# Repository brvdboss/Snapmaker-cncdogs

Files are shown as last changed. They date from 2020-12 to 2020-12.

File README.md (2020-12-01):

# Snapmaker-cncdogs
 clamping dogs for the cnc wasteboard of the snapmaker2
 
 This provides a set of clamping tools to secure your stock on the snapmaker cnc wasteboard.
 There are variants for the small holes (where the screws go to mount the wasteboard) and the larger holes where the provided clamps fit
 
 The spirals are used to put additional pressure on one side and come in different sizes to adjust for all your clamping needs
 For these the "keys" are used to make them universal for every type of hole in the wasteboard.  The smallest spiral is designed so it can be used on the holes closest to the side and still clear the vertical axes.
 
 To tighten the clamps a handle is provided to make that easier with the same keyhole.
 This handle can also be used as a wedge to secure your material.

 An additional version has been added with a through-hole that fits an m4 screw. this allows to fix the "large" dogs & turnkeys to fixed to the board.  This improves the clamping force significantly. and eliminates the risk of the dogs coming loos through vibration.  It does mean clamping is no longer "toolless"
 The screws are countersunk rather deep to minimize the risk of your drill hitting it if you go through the plastic and this also helps with the rigidity as the screwhead provides additional strenght in the doghole.

## Why use this?
If you have a piece of material that you can't clamp from the top down or need to secure from the side, for example to align it more easily.
It's from plastic. If your bits do drill in to this, they probably won't get damaged.

## Overview of elements
- **cornerdog**: element to fix the corner of your material. Both in large and small hole variant. For the large version there is now also a through-hole version.
- **dog**: align on the side of your material. Both in large and small hole variant. For the large version there is now also a through-hole variant.
- **spiralhandle**: handle to tighten the pressurespirals.  You can also use this as a wedge in combination with a dog to the fix the material.
- **turnkey**: the "key" that locks in the holes. Both in a large and small hole variant. For the large version there is now also a through-hole variant.
- **turnkeyspiral**: the actual pressure spiral, insert a key, put it in the hole and turn with the spiralhandle.  Different sizes available

Where possible all objects are parameterized so they can easily be adjusted in size
There are no throughole variants of the small versions of the clamps as those holes are used to mount the wasteboard.

## What to watch out for when using this
- These clamps only apply pressure from the side. Depending on the material, tolerance in your dogholes.  Often the material has a tendency to be pushed upwards.  The through hole versions mostly minimize this, but require M4 screws
- The holes in the waste board are small and not very deep, in addition the waste board is rather soft.  Don't put huge amounts of pressure on it.
- When fixing your material also push it down while clamping and check you push the dogs down to make sure everything is secure. You could use one of the snapmaker provide clamps to push down on the pressure weels to get some more downforce on the material.
- You can use the M4 screws included with the snapmaker to fixate the through-hole versions. They are just long enough, a tiny bit longer would have been conventient though.

## How to print
Printing everything using the defaul fast profile in Luban seems to work fine and everything fits snuggly together. (tested with snapmaker provided white filament)

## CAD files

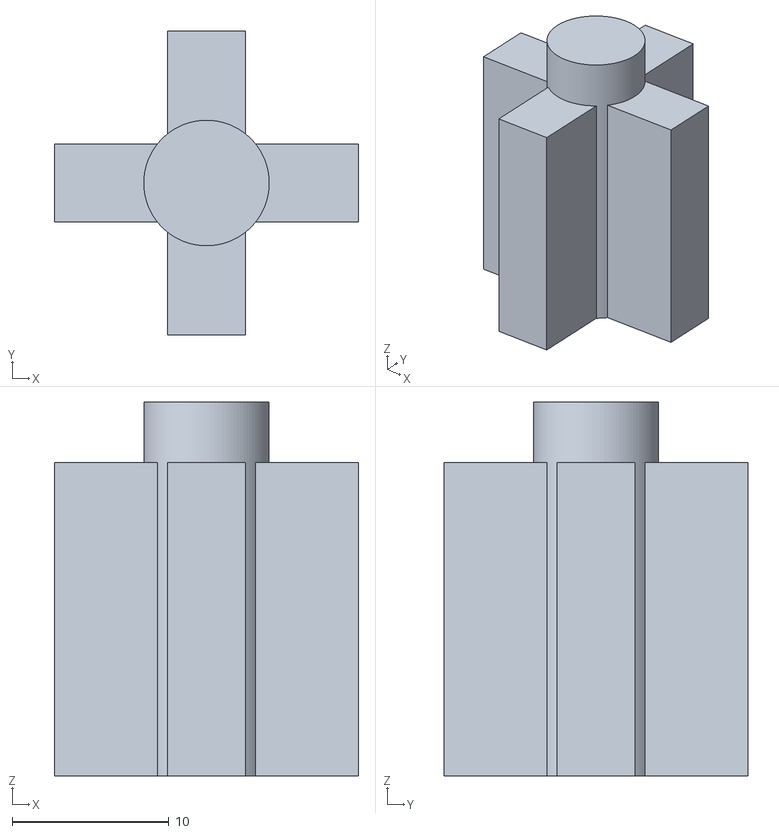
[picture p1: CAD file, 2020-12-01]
stl/turnkeysmall.stl
19.4 x 19.4 x 23.9

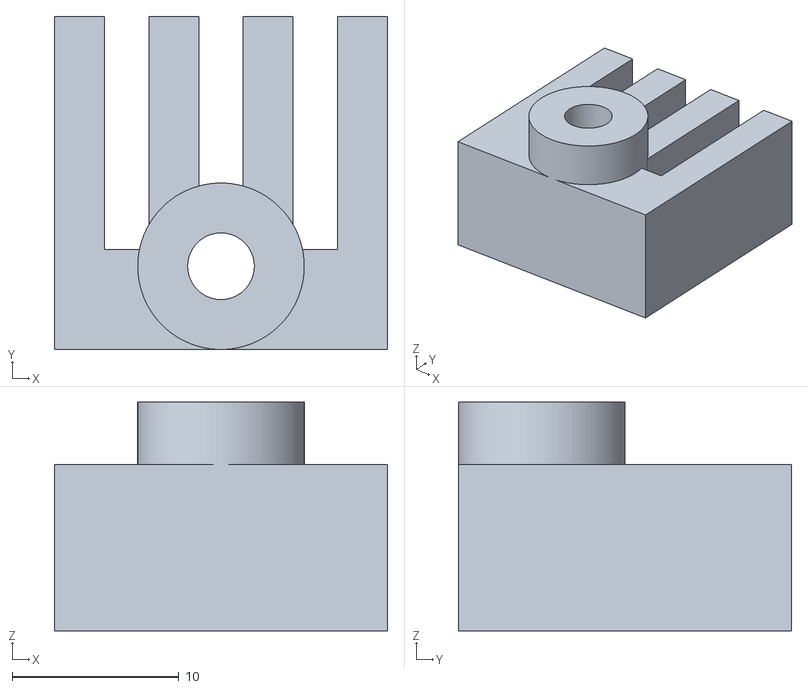
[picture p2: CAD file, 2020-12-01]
stl/doglarge-hole.stl
20.0 x 20.0 x 13.8

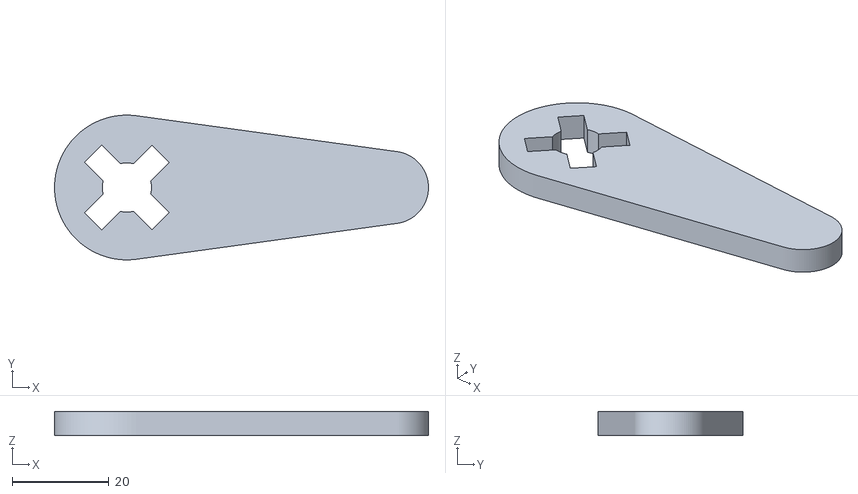
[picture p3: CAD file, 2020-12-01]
stl/spiralhandle.stl
77.5 x 30.0 x 5.00

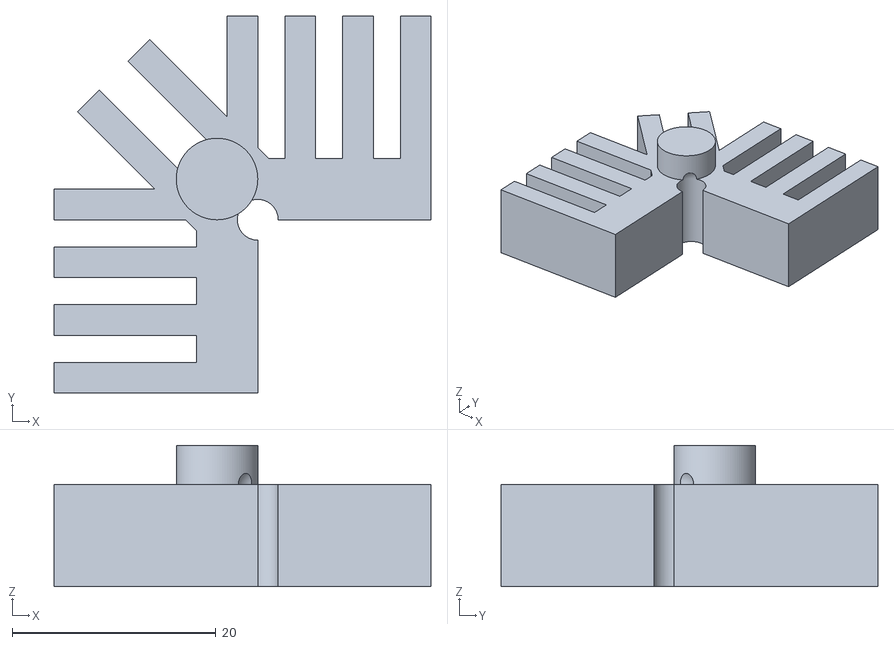
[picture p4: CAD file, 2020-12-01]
stl/cornerdogsmall.stl
37.0 x 37.0 x 13.8

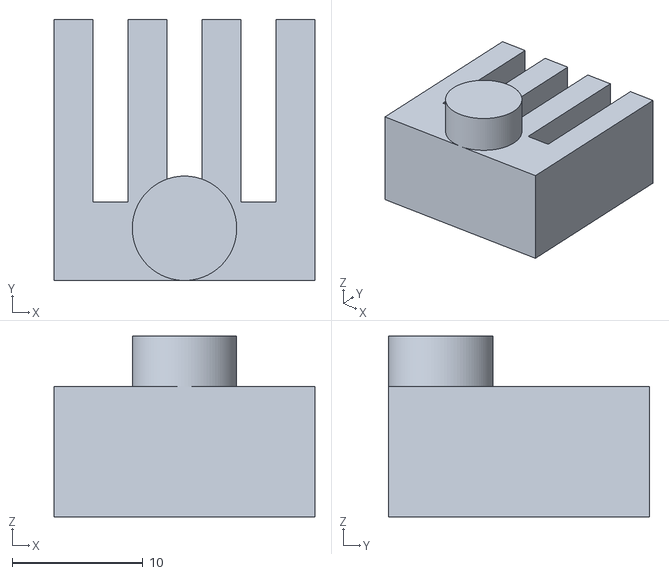
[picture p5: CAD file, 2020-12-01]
stl/dogsmall.stl
20.0 x 20.0 x 13.8

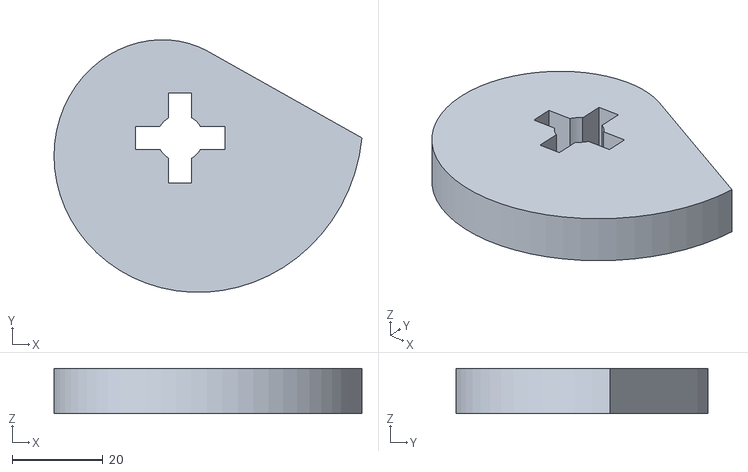
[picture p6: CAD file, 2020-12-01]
stl/turnkeyspiral-40_15.stl
67.8 x 55.5 x 10.0

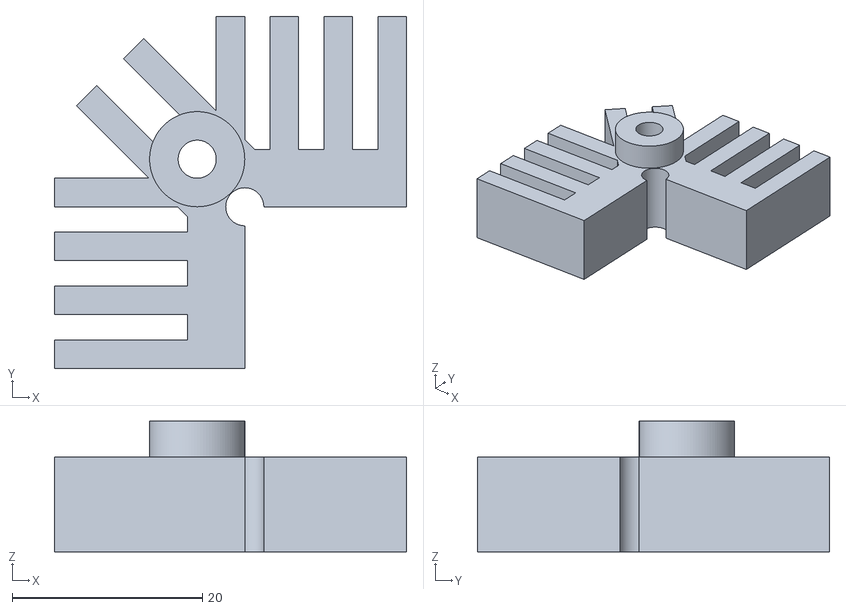
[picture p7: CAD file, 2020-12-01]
stl/cornerdoglarge-hole.stl
37.0 x 37.0 x 13.8

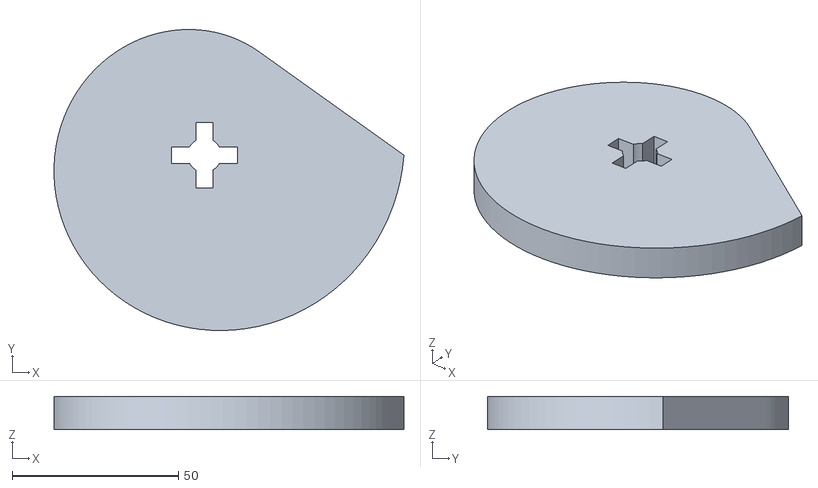
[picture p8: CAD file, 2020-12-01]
stl/turnkeyspiral-60_30.stl
105.2 x 90.5 x 10.0

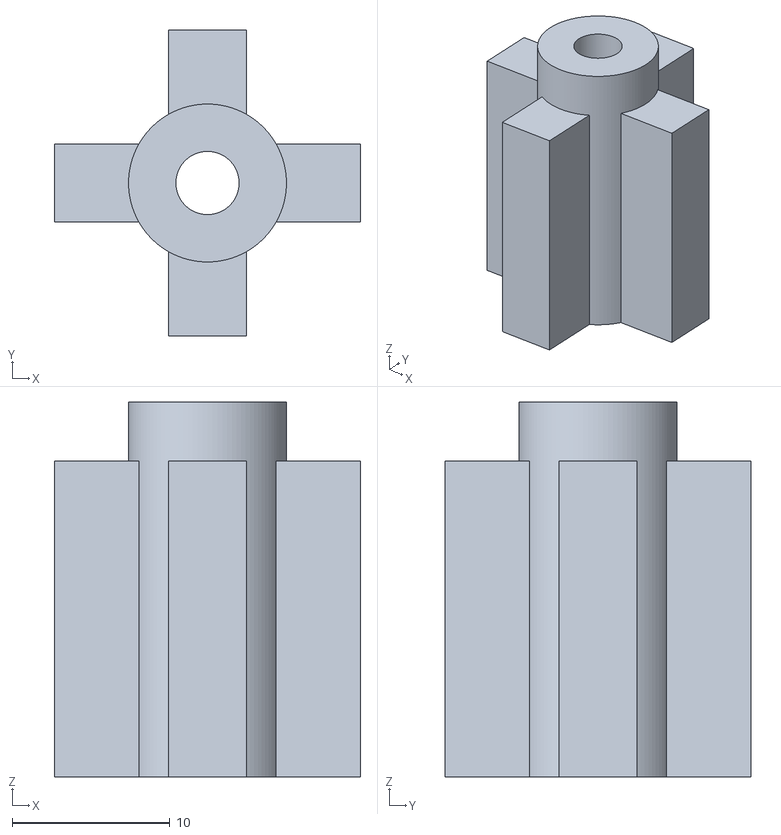
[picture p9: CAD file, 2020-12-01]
stl/turnkeylarge-hole.stl
19.4 x 19.4 x 23.8

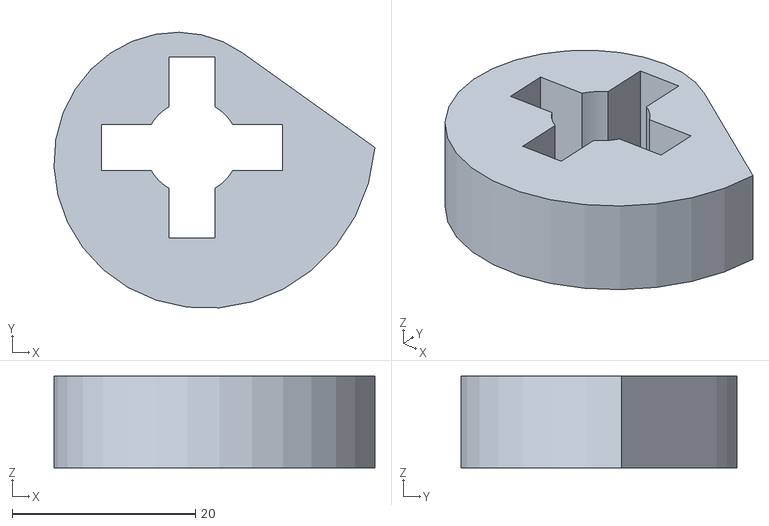
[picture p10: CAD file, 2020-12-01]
stl/turnkeyspiral-20_10.stl
35.1 x 30.1 x 10.0

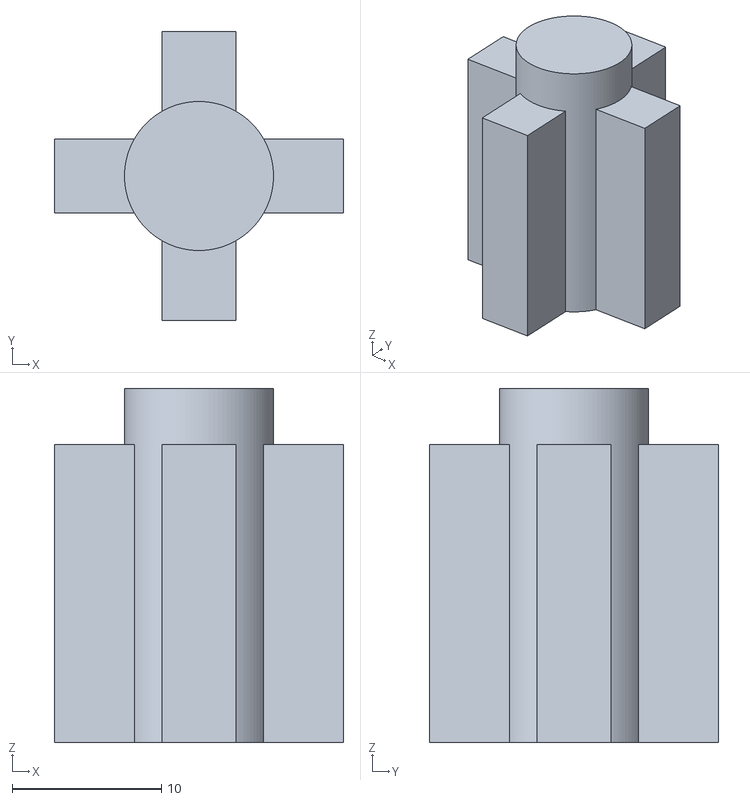
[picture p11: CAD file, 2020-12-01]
stl/turnkeylarge.stl
19.4 x 19.4 x 23.8

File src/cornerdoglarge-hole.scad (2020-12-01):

include <lib/dogs.scad>

cornerdog(dogblock, type="large", hole=true);

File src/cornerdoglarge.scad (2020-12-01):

include <lib/dogs.scad>

cornerdog(dogblock, type="large", hole=false);

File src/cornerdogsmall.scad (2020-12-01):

include <lib/dogs.scad>

cornerdog(dogblock, type="small", hole=false);

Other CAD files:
stl/doglarge.stl
stl/cornerdoglarge.stl
src/doglarge-hole.scad
src/doglarge.scad
src/dogsmall.scad
src/spiralhandle.scad
src/turnkeylarge-hole.scad
src/turnkeylarge.scad
src/turnkeysmall.scad
src/turnkeyspiral-20_10.scad
src/turnkeyspiral-40_15.scad
src/turnkeyspiral-60_30.scad

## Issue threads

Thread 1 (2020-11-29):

pressure spiral: make flat edges depend on size

brvdboss, 2020-11-29:
The pressure spirals have small flat edges to improve the friction when clamping and prevent them from getting loose from vibrations.  It might be better to have them depend on the total size of the pressure spiral.  They should have a fixed width, now they become wider with a bigger spiral.

brvdboss, 2020-12-01:
The flat edge has been adjusted so that it's max 2mm at the biggest diameter.  This for all sizes of spirals

Closed 2020-12-01.

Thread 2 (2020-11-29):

Make everything through hole so it can be fixed with the screws

brvdboss, 2020-11-29:
It should be possible to make all clamps through hole (instead of using the little guide pin that doesn't serve a real purpose).
The could still be used without a screw.
but on some strategic places we can the still insert a screw  to fix it more better in place. This should also help with keeping things down on the plate.

brvdboss, 2020-12-01:
Through hole versions have been committed and seem to work great. Hardly any upward lift remaining when using the through hole versions

Closed 2020-12-01.

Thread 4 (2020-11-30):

spiral and turnkey don't fit well together

brvdboss, 2020-11-30:
See https://forum.snapmaker.com/t/printed-cnc-clamps-sideways-feedback-welcome/11993/8

too tight of a fit of the spiral & turnkey.  Instead of using a scaling percentage in the code, use absolute size difference.  I don't think it is strictly necessary to have an extreme tight fit of these components. So better be on the safe side.

brvdboss, 2020-12-01:
made some tiny adjustments and remeasured everything extensively.  Everything should fit a expected.  Tolerances are a tiny bit higher now.

Closed 2020-12-01.

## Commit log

2020-11-29 First version of everything
    Initial commit of the dogs collection
    [cornerdoglarge.scad, cornerdoglarge.stl, cornerdogsmall.scad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]
2020-12-01 increase tollerances for fitting parts together
    #4 increase the tolerances on the fitting of the spiral and turnkey. If the old one did fit, the new ones should fit as well with previously printed parts
2020-12-01 Update dogs.scad
    #2 remove the mini cylinders. they were purely cosmetic and will be replaced with a through hole anyway
2020-12-01 through holes
    #2
    adding holes to cornerdogs and normal dogs
    still struggling with the turnkey (are those really necessary anyway?)
2020-12-01 fixing through hole in turnkey
    #2 fixingbug in turnkey
    debugging is fun
2020-12-01 regenerate all the stls
    #4 #2 #1
    regenerall stl files for the adjustments made and adding last newlines to the files
    [cornerdoglarge-hole.scad, cornerdoglarge-hole.stl, cornerdoglarge.scad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]
2020-12-01 parallisation of stl generation
    Execute the generation of all files in parallel, what else is 16 thread cpu good for
2020-12-01 update readme with info on the through hole variant
    #2 update readme with changes on the through hole variants.
    [cornerdoglarge-hole.stl, cornerdoglarge.stl, cornerdogsmall.stl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]
